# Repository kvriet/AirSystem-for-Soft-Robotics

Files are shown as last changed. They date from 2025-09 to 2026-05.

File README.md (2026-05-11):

# AirSystem for Soft Robotics
Modular Air System for Soft Robotics\
Designed and created by [C.M. van Riet](https://research.tue.nl/en/persons/cm-katrien-van-riet) - Summer 2025\
With thanks to d.search at Eindhoven University of Technology for their guidance.\
Special thanks to Geert van den Boomen for checking the schematics and debugging the circuits.

## The system
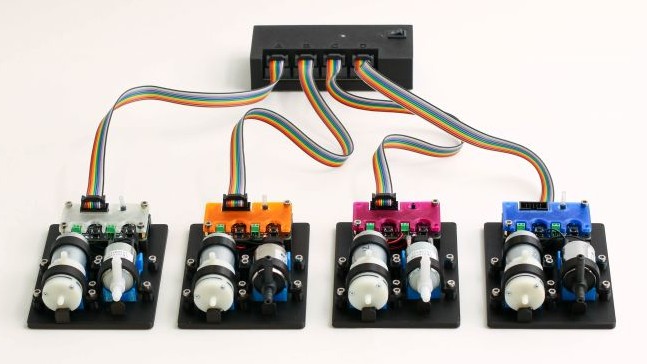
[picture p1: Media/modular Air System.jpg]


**AirSystem** was designed as a low-cost way to rapidly prototype with air, costing roughly €125 for the entire system. AirSystem consists of 1 controller and 4 pneumatic units. Each pneumatic unit contains one pump, one solenoid valve, and one pressure sensor. The board provides 12V power and as such, any pump or solenoid that requires 12V power can be attached to the unit board. 

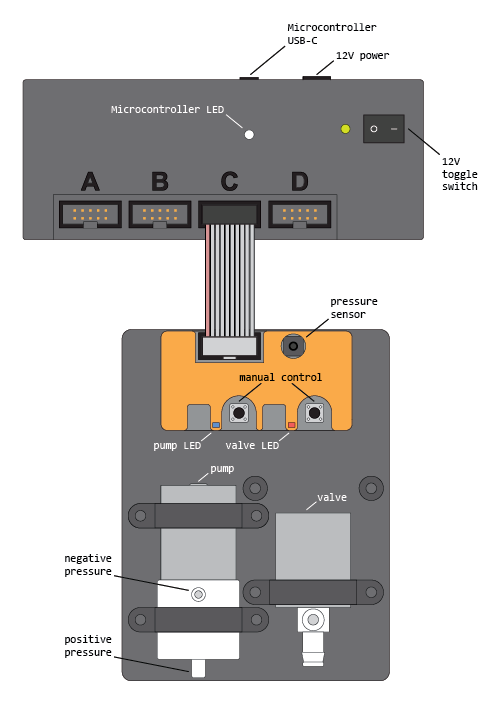
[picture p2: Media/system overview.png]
System overview


### Pneumatic Components
For the pneumatic board, easy-to-find components are used:
1. Pump 370A, 12V, 3.2LPM
2. Solenoid valve Skoocom SC0829GW, 12V
3. MCP-H10 pressure sensor, 0-200kPa, 3.3V

### Manual
A manual for AirSystem describes in detail how the system works and how the Arduino library can be installed: [AirSystem Manual](https://github.com/kvriet/AirSystem-for-Soft-Robotics/blob/main/Air%20System%20manual%20v1.4.pdf)
Users are free to connect the sensor, pump, and valve to their inflatables as desired. However, a sample pneumatic circuit is outlined in the manual, along with example Arduino sketches that work well with such a circuit.

## Arduino Library
The system is controlled by a Waveshare RP2040 Zero and can be programmed through the Arduino IDE with a custom library: [AirSystem](https://github.com/kvriet/AirSystem-for-Soft-Robotics/tree/main/Arduino%20library/AirSystem) This folder should be placed in the libraries folder of the Arduino folder. 

The library comes with 7 examples that showcase the abilities of **AirSystem**:
  1. Manual control
  2. Pressure reading
  3. Pump control
  4. Valve control
  5. Pump control without delay
  6. Haptic effects
  7. Object arrays

The video below shows such a haptic effect:

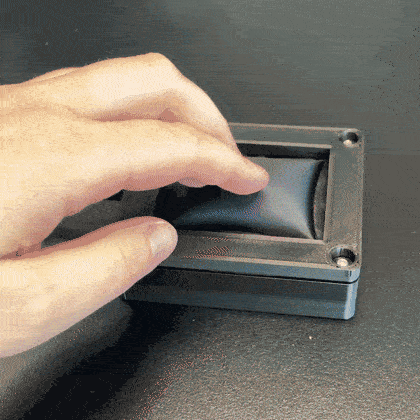
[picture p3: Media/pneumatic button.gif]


## Schematics and KiCAD Files
The schematics for this project and the KiCAD files can be found here: [KiCAD folder](https://github.com/kvriet/AirSystem-for-Soft-Robotics/tree/main/KiCAD).

## 3D Printing Files
The STLs for this project can be found here: [Design Files](https://github.com/kvriet/AirSystem-for-Soft-Robotics/tree/main/Design%20Files).
- The prints will fit most regular printers and can be printed out of PLA, 0.3 layer height, 4 perimeters (walls), 20% infill. The cushions for the pumps and solenoids are printed in TPU. These cushions can be replaced with some sponge (simple kitchen sponges work well) if TPU printing is not an option.
- To minimise vibrations and prevent the cases from sliding around on a hard surface, 6mm silicone feet are added to the bottom of control and follower cases.
- Any 4mm holes in the prints will require M3x4mm heated inserts to create screw holes. These can be inserted with a soldering iron at roughly 300 degrees Celsius. The other 3mm holes are self-tapping.

The screws needed for these cases are:

**Controller**
- 4x M3x10 or M3x20 (any length in between), flathead

**Follower**
- 4x M3x6 for the coloured cover
- 4x M3 spacer: 6mm height, 6mm thread
- 8x M3x10 for the clamps

## Limitations
- Although protection is implemented on the signal lines, the Waveshare RP2040 Zero sometimes dies when the IDC connector cable is plugged into the controller or follower when the RP2040 is still connected by USB C. For this reason, it is important to unplug the RP2040 before plugging in/out ribbon cables.
- Due to the above issue, I am looking into switching to the ESP32 C3 Zero (Pro). This board is equally cheap, but seems to be more robust. This board is currently not yet a drop-in replacement for the RP2040, although it can already be made to work if some soldering on the controller is reworked and the pin numbers in the library are updated. I will probably release KiCAD files for an ESP32 controller in the future. The follower boards will not be affected, although the resistor value in series with the mosfet might be updated (from 1k to 500R).
- The Skoocom solenoid valve is able to remain closed up to pressures of 100kPa, whereas the pump is able to deliver 150kPa. This means the valve will start leaking at pressures over 100kPa. In practice, this is not a major issue, as our projects rarely need pressures of over 100kPa (usually maxing out at 50kPa for haptic purposes). However, this overpressure might reduce valve longevity in the long run. In the future, a higher-pressure solenoid valve could be found, or a pump could be found that delivers max 100kPa. This would also allow for a lower-range pressure sensor to be used, the MCP-H10 0-100kPa, 3.3V. Switching to the 0-100kPa sensor would also double pressure measuring resolution.
- Currently no PID has been implemented in the library. As many inflatables or the tubing used are somewhat elastic, I have found that setting a target pressure (feedback loop sensor reading to pump power) is enough to achieve that pressure with a minimal offset. However, for more high-end applications, PID should be implemented.
- The Skoocom solenoid valve is not proportional. It is just open/closed. This means that controller deflation is a challenge. This can be worked around by turning on the pump simultaneously to opening the valve to reduce the air flowing out. Additionally, a resistor (very thin tube) could be connected to the valve outlet to reduce airflow out of the system. However, such a resistor also slows down response times when air does need to evacuate the system quickly. This is a trade-off for how cheap this entire system is.

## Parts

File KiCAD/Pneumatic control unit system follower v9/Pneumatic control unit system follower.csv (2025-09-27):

Reference | Value | Datasheet | Footprint | Qty | DNP
C1,C2,C3,C4,C7,C8,C11 | 100nF | ~ | Capacitor_SMD:C_0603_1608Metric_Pad1.08x0.95mm_HandSolder | 7
C5,C6,C9,C10 | 100uF | ~ | Capacitor_THT:CP_Radial_D6.3mm_P2.50mm | 4
D1,D3 | LED_Small | ~ | Diode_SMD:D_0805_2012Metric_Pad1.15x1.40mm_HandSolder | 2
D2,D4 | 1N4007 | http://www.vishay.com/docs/88503/1n4001.pdf | Diode_SMD:D_SMA_Handsoldering | 2
D5,D6 | 1N4148 | https://assets.nexperia.com/documents/data-sheet/1N4148_1N4448.pdf | Diode_SMD:D_MiniMELF_Handsoldering | 2
J1 | unit_1 | https://www.tinytronics.nl/en/cables-and-connectors/connectors/jst-compatible/jst-xh-6p-compatible-pcb-connector-male-90 | Library:JST_XH_S6B-XH-A-1_1x06_P2.50mm_Horizontal_5mm | 1
M1,M2 | Pump | ~ | TerminalBlock_Phoenix:TerminalBlock_Phoenix_MPT-0,5-2-2.54_1x02_P2.54mm_Horizontal | 2
Q1,Q2 | AO3400A | http://www.aosmd.com/pdfs/datasheet/AO3400A.pdf | Package_TO_SOT_SMD:SOT-23 | 2
R1,R4 | 680R | ~ | Resistor_SMD:R_0603_1608Metric_Pad0.98x0.95mm_HandSolder | 2
R2,R5 | 330R | ~ | Resistor_SMD:R_0603_1608Metric_Pad0.98x0.95mm_HandSolder | 2
R3,R6 | 100k | ~ | Resistor_SMD:R_0603_1608Metric_Pad0.98x0.95mm_HandSolder | 2
SW1,SW2 | SW_Push | ~ | Button_Switch_THT:SW_PUSH_6mm | 2
U1 | ~ |  | Library:MCP-H10 | 1

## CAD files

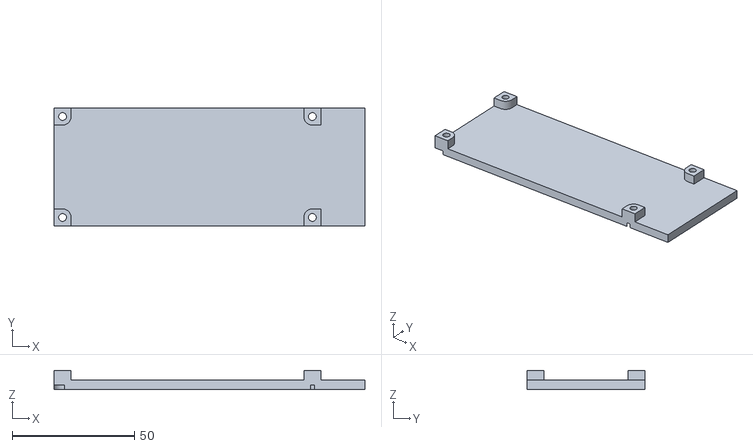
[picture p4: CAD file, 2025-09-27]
Design Files/bottom lid v2.2.stl
127.1 x 48.3 x 7.80

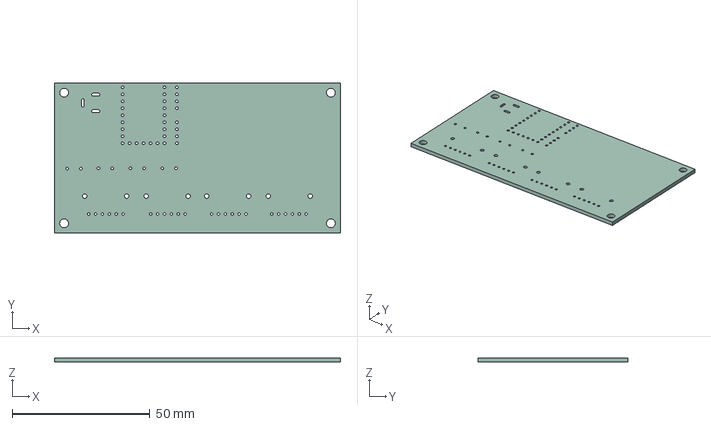
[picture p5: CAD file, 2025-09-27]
KiCAD/Pneumatic control unit system leader v9/Pneumatic control unit system.step
104.0 x 54.5 x 1.60 mm

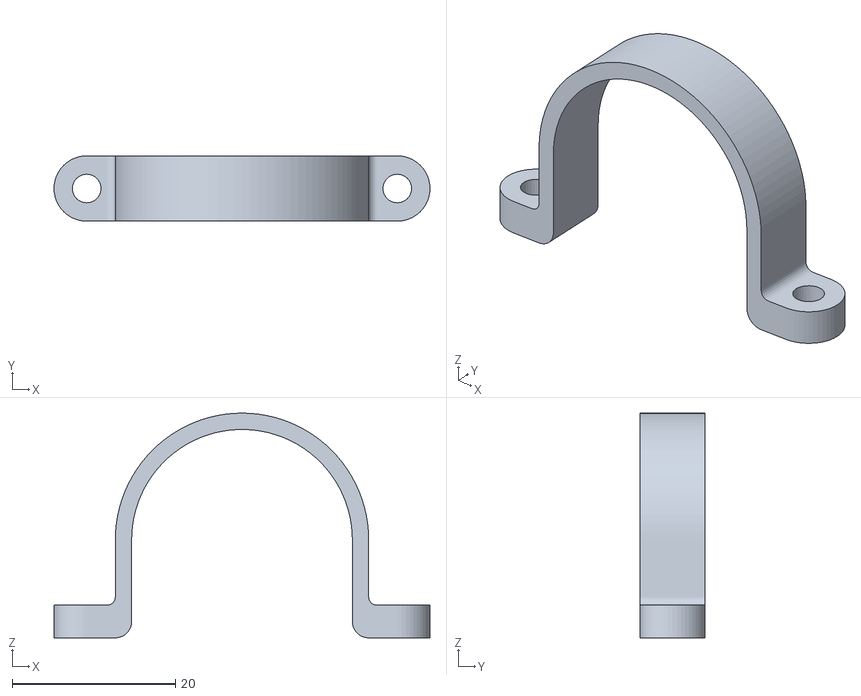
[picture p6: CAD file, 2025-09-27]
Design Files/clamp big v5.stl
46.0 x 8.00 x 27.5

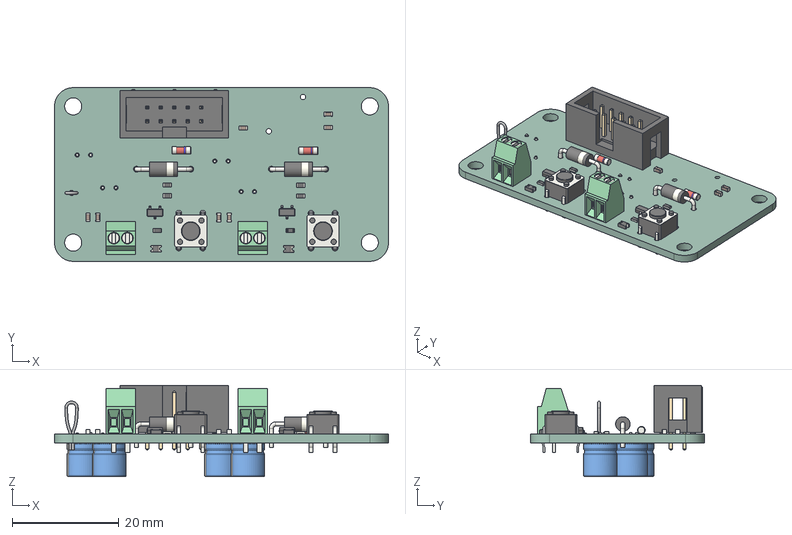
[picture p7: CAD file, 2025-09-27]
KiCAD/Pneumatic control unit system follower v9/follower v8.2.step
62.5 x 32.5 x 17.1 mm
R_0603_1608Metric x 6
D_MiniMELF_Standard x 2
D_DO-41_SOD81_P10.16mm_Horizontal x 2
SW_PUSH_6mm x 2
TestPoint_Loop_D2.50mm_Drill1.0mm
C_0603_1608Metric x 7
IDC_Header_2x05_P254mm_Vertical
TerminalBlock_Phoenix_MPT_05_2_254_1x02_P254mm_Horizontal x 2
SOT_23 x 2
D_0805 x 2
CP_Radial_D63mm_P250mm x 4
Pneumatic control unit system_PCB

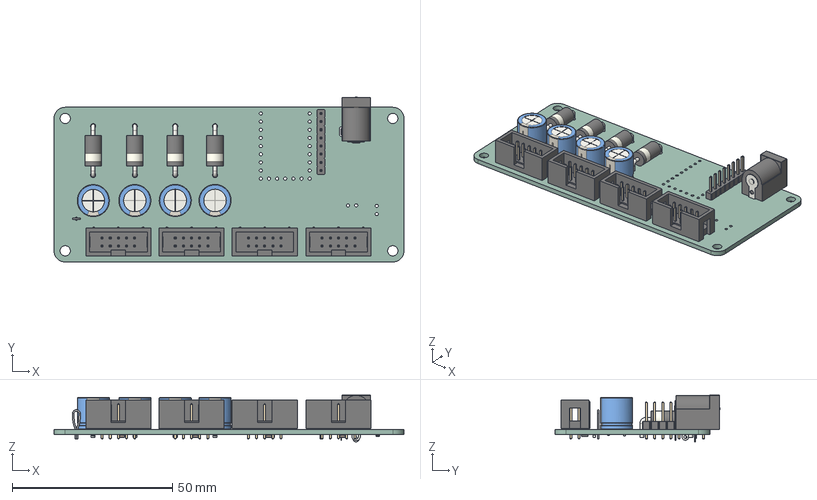
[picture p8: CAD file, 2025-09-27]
KiCAD/Pneumatic control unit system leader v9/Leader v9.step
109.1 x 51.5 x 14.6 mm
IDC_Header_2x05_P254mm_Vertical x 4
TestPoint_Loop_D2.50mm_Drill1.0mm
CP_Radial_D100mm_P500mm x 4
D_DO-201AD_P15.24mm_Horizontal x 4
PinHeader_1x08_P254mm_Vertical
BarrelJack_Horizontal
R_0805_2012Metric
C_0603_1608Metric x 5
Pneumatic control unit system_PCB

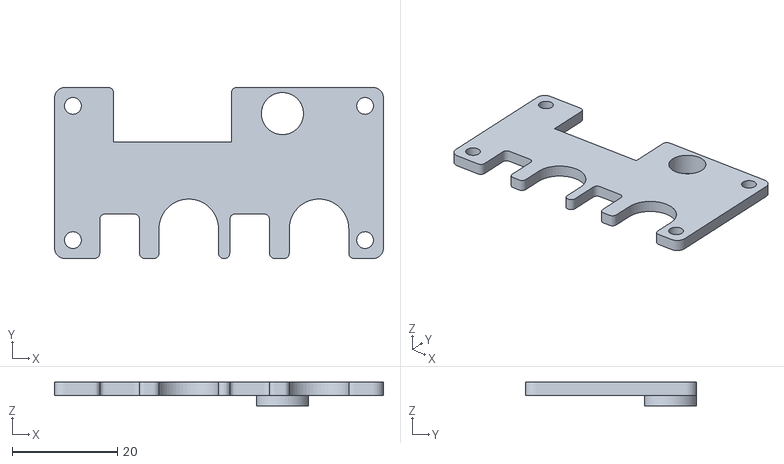
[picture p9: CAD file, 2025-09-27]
Design Files/top lid PLA v2.2.stl
62.5 x 32.5 x 4.50

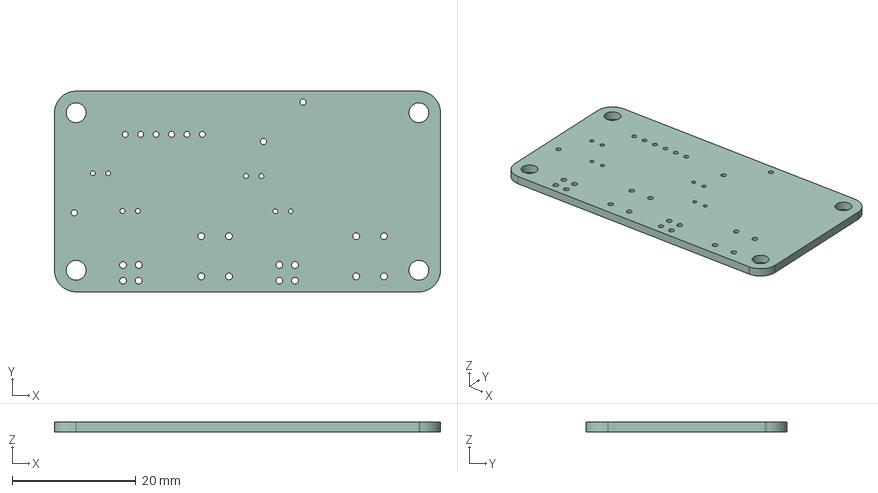
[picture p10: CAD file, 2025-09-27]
KiCAD/Pneumatic control unit system follower v9/Pneumatic control unit system broad.step
62.5 x 32.5 x 1.60 mm

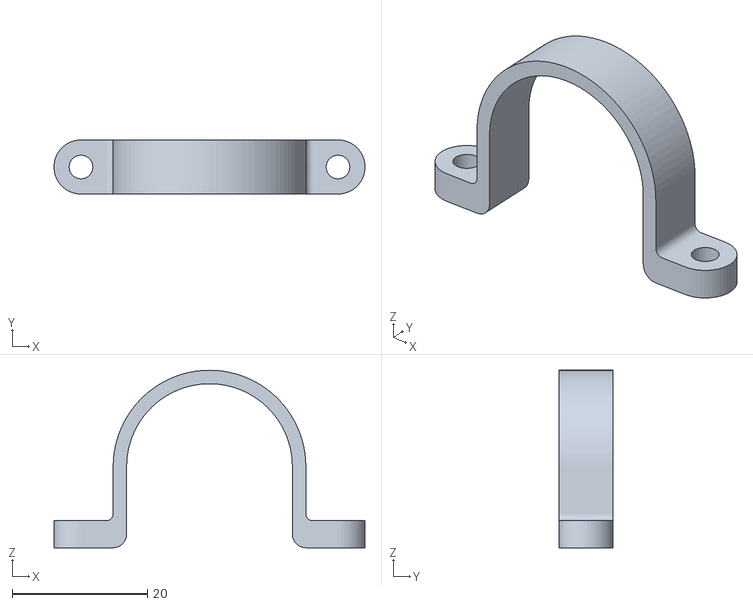
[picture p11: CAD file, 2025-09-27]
Design Files/clamp small v5.stl
46.0 x 8.00 x 26.2

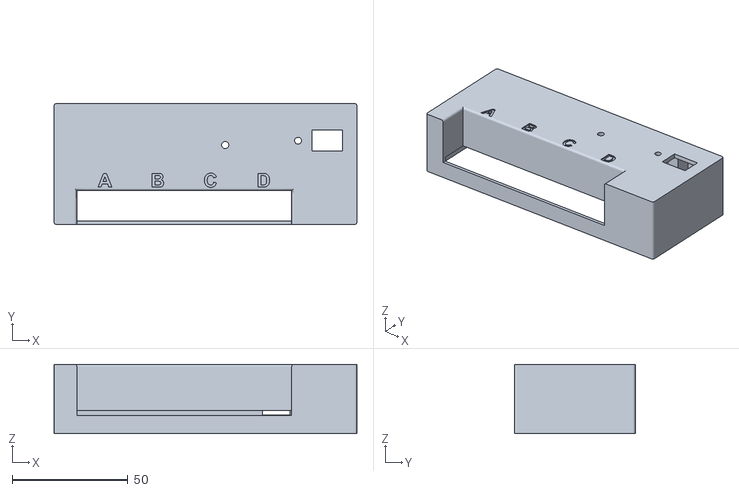
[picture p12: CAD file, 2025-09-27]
Design Files/top lid v2.3.stl
131.1 x 52.2 x 30.0

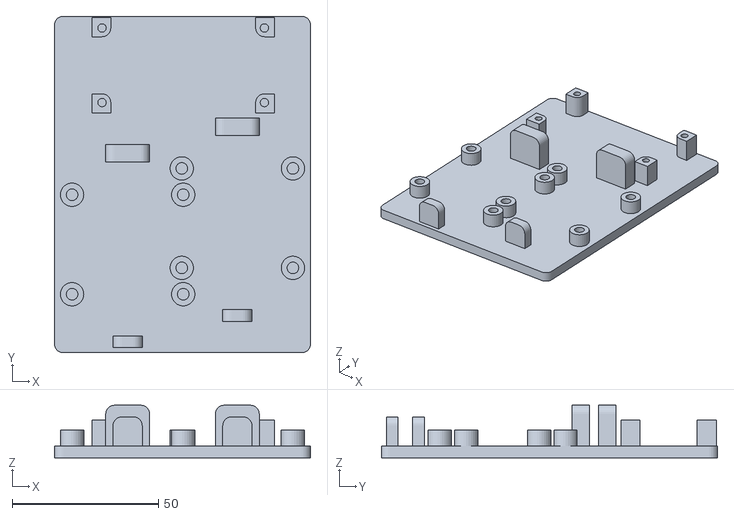
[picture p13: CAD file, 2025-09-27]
Design Files/case base v2.1.stl
87.5 x 115.0 x 18.0

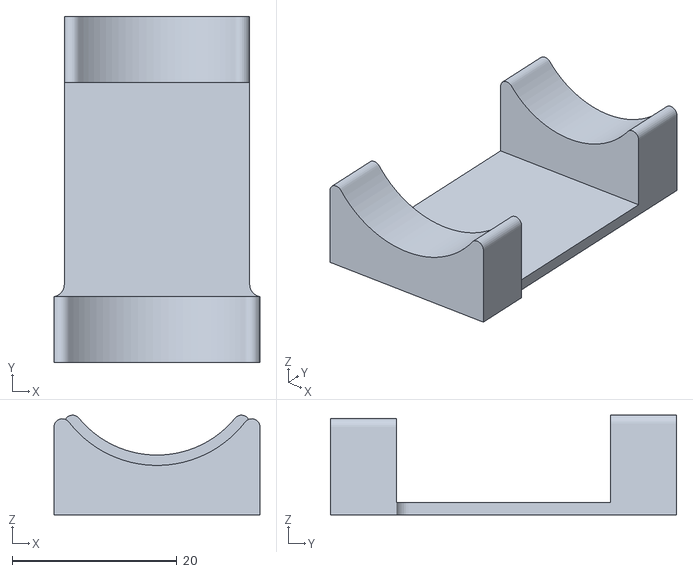
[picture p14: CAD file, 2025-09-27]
Design Files/cushion connected v2.stl
25.0 x 42.0 x 12.1

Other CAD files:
KiCAD/Pneumatic control unit system follower v9/follower v8.step

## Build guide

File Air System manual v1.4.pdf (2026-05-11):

# AIR CONTROL SYSTEM

# MANUAL

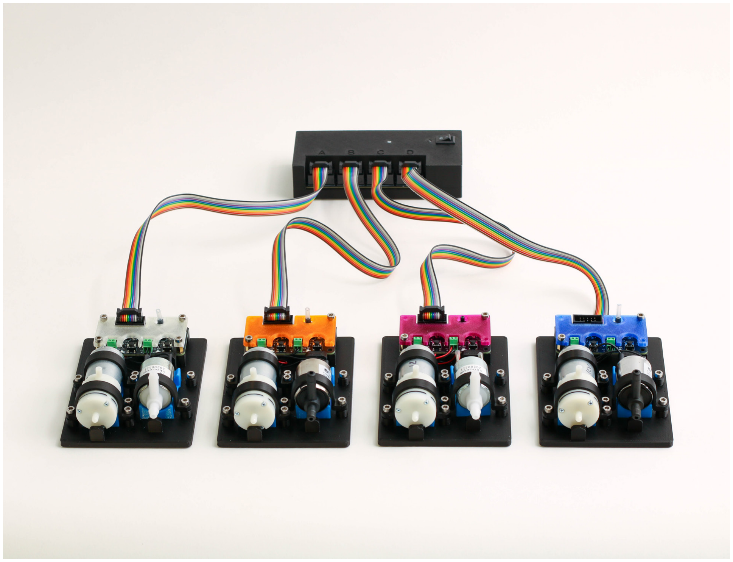
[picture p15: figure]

C.M. van Riet - May '26 - v1.4

# OVERVIEW

Controller
The controller can control up to 4 pneumatic units. It is powered by a 12V power supply and a Waveshare RP2040 PiZero, which can be

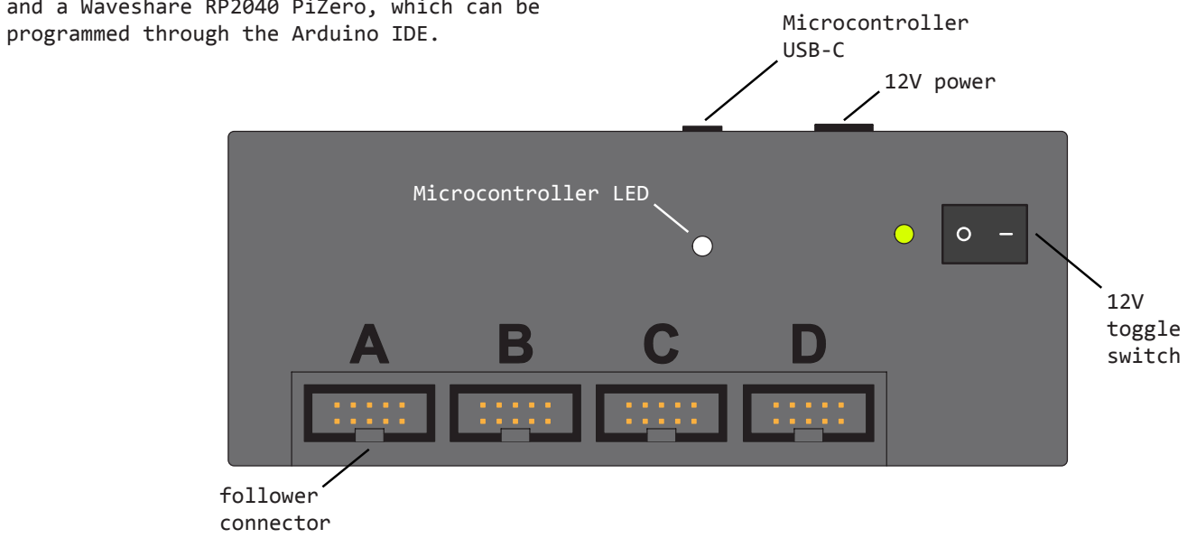
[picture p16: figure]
programmed through the Arduino IDE.; 12V power; Microcontroller USB-C; follower connector; 12V toggle switch; Microcontroller LED

Pneumatic unit

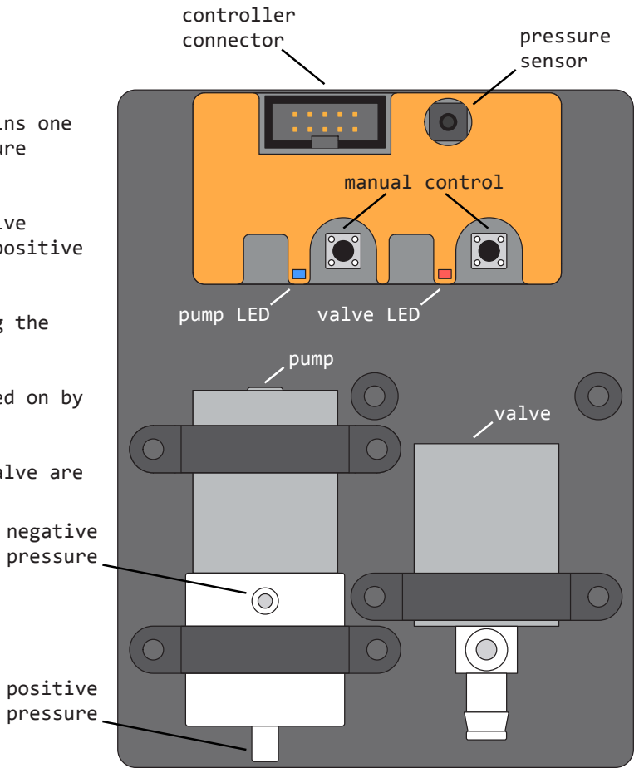
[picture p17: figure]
controller; connector; pressure; sensor; pump LED; pump; valve; valve LED; manual control; positive pressure; negative pressure

Each pneumatic unit (or follower) contains one pump, one solenoid valve, and one pressure sensor.

The pump can provide positive and negative pressure (vacuum). You will mainly use positive pressure for the pneumatic buttons.

The valve is normally closed. Activating the valve opens it.

The pump and valve can be manually turned on by pressing the buttons.

The LEDs indicate whether the pump or valve are turned on.

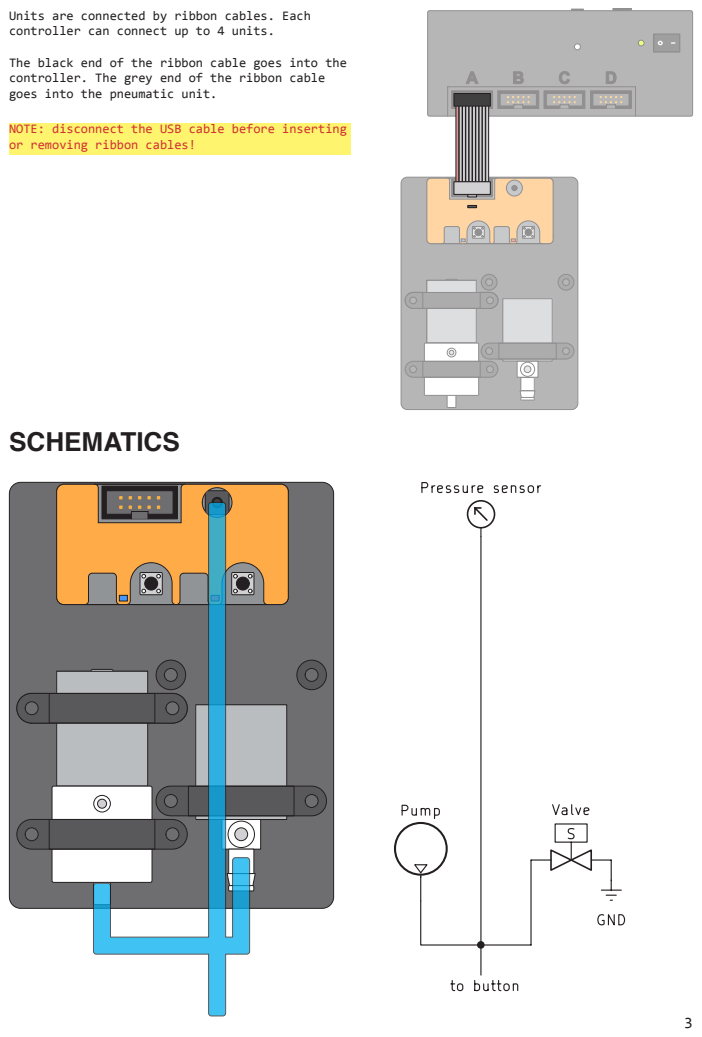
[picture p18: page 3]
SCHEMATICS

Units are connected by ribbon cables. Each
controller can connect up to 4 units.
The black end of the ribbon cable goes into the
controller. The grey end of the ribbon cable
goes into the pneumatic unit.

NOTE: disconnect the USB cable before inserting
or removing ribbon cables!

# INSTALLING THE BOARD

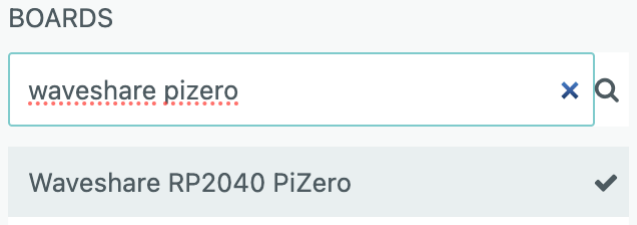
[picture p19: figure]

# INSTALLING THE ARDUINO LIBRARY

Before you can upload sketches to the AirSystem, you need to install the correct microcontroller board. The system uses the Waveshare RP2040 PiZero board.

Open Arduino IDE. Go to Settings (ctrl + , or command + ,).
In the Additional boards manager URLS, add this link:
https://github.com/earlephilhower/arduino-pico/releases/download/4.5.2/package_rp2040_index.json
Now go to Boards Manager:

Search for and install "Raspberry Pi Pico/RP2040/RP2035" by Earle F. boards.

To connect to the board, click the board connector:

Search for "waveshare pizero" and select the "Waveshare RP2040 PiZero":

Before you can make Arduino sketches using the AirSystem library, you need to install the library.

To do this, put the AirSystem folder (unzipped) into your Arduino libraries folder:

Arduino/
└── libraries/
└── AirSystem/
├── AirSystem.h
├── AirSystem.cpp
└── examples/

Whenever you want to use the library, don't forget to call it at the top of your sketch: #include <AirSystem.h>

Also don't forget to initialise the pins in the setup loop:
AirSystem_begin(); // Initialise the pins

# PROGRAMMING

The AirSystem library is an object-oriented library that provides three types of objects:
- Pump → controls an air pump using PWM (0–100% power).
- Valve → controls a solenoid valve (open/close).
- Sensor → reads air pressure from a pressure sensor.
Accessing Objects
You can access objects in two ways:
By name (if you created them individually):
- PumpA.set(50); | // Set PumpA to 50% power
- ValveB.open(); | // Open ValveB
- float p = SensorC.read(); // Read SensorC pressure

By array index:
- pumps[0].set(50); | // PumpA
- valves[1].close(); | // ValveB
- float p = sensors[2].read(); // SensorC Functions
Pump
- set(percentage) → Set pump power (0–100%).
- off() | → Turn pump off (same as set(0)).
- on() | → Turn pump fully on (100%).

Valve
- open() | → Open the valve.
- close() | → Close the valve.

Sensor
- read() | → Returns the current pressure in kPa (kiloPascal).

# STEP 1: MANUAL CONTROL

The pump and valves can be operated through the push buttons on the follower unit.

Upload the following code. It will not activate the pumps or valves. Instead you can press the pump and valve buttons to inflate and deflate your pneumatic button.

/*
AirSystem Demo Sketch

Author: C.M. van Riet
Library: AirSystem
Date: September 2025

Objects can be called in 2 ways:
- pumpA, valveB, sensorC (named)
- pumps[0], valves[1], sensors[2] (array-based)

Functions available in this library:
- Initialize the system with AirSystem_begin()
- Control pumps with .set(percentage), on(), and .off()
- Control valves with .open() and .close()
- Read pressure from sensors with .read()

Hardware:
- Designed for a maximum of 4 pumps, 4 valves, and 4 sensors
- Pin mappings are fixed in the library (see AirSystem.h)

Notes:
- Make sure to include the AirSystem.h library at the top of your sketch (#include <AirSystem.h>)
- This example can be found under File > Examples > AirSystem > 1_First_demo.

Board:
- Add this link to preferences, Additional boards manager URLs: https://github.com/earlephilhower/arduino-pico/releases/download/4.5.2/package_rp2040_index.json
- Install "Raspberry Pi Pico/RP2040/RP2035" by Earle F. boards
- Connect to Waveshare RP2040 PiZero
*/

#include <AirSystem.h>

void setup() {
Serial.begin(9600);
AirSystem_begin(); // Initialise the pins
pumpA.off(); | // Pump off
valveA.close(); | // Close valve
}

void loop() {
// This loop is empty
// You can turn on the pump and valve by pressing // the buttons on the board of the unit
}

#include <AirSystem.h>

void setup() {
Serial.begin(9600);
AirSystem_begin(); // Initialise the pins
pumpA.off(); | // Pump off
valveA.close(); | // Close valve
}

void loop() {
float pressure = sensorA.read();
Serial.print(0); // Lower limit in Serial Plotter Serial.print("\t"); // Print a tab Serial.print(200); // Upper limit in Serial Plotter Serial.print("\t"); // Print a tab Serial.println(pressure);

delay(10);
}

# STEP 2: PRESSURE READINGS

To get the pressure sensor value, use the read() function.

Upload the following code. Use the push buttons to inflate and deflate your pneumatic button and use the Serial Monitor (Ctrl+Shift+M) and Serial Plotter to watch the pressure value fluctuate.

# STEP 3: PUMP CONTROL

The code below turns the pump on and off. Don't connect the pump to your pneumatic button yet!

- Try to change the delay values. How does the pump turning on and off change?
- Try to change the value in the set() function. How does it change the pump behaviour?
- If you connect the pump to your pneumatic button, will it only inflate? Or also deflate?

#include <AirSystem.h>

void setup() {
Serial.begin(9600);
AirSystem_begin(); // Initialise the pins
pumpA.off(); | // Pump off
valveA.close(); | // Close valve
}

void loop() {
pumpA.set(50);
Serial.println("Pump set to 50% intensity");

delay(2000);

pumpA.off();
Serial.println("Pump turned off");

delay(2000);
}

#include <AirSystem.h>

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

void loop() {
valveA.close();
pumpA.set(25);
Serial.println("Valve closed and pump set to 25%");

delay(1000);

valveA.open();
pumpA.off();
Serial.println("Valve opened and pump turned off");

delay(2000);
}

# STEP 4: VALVE CONTROL

The code below is similar to the code in step 3, but it adds valve control. Now your pneumatic button will inflate and deflate.

- Play with the pump power percentage and the timing (delay) to get an aesthetically pleasing inflation and deflation of your pneumatic button.

# STEP 5: PUMP WITHOUT DELAY

In step 4 we turned the pump on and off. We used the delay() function for this, but this freezes up the entire program; you can't do anything else during the delay. To fix this, the code below gives you pump control without delay. This is similar to the 'Blink without delay' example in the Arduino library.

For this to work, we use a general timer (currentMillis) to keep track of time.

// Pump without delay based on the code by David A. Mellis

#include <AirSystem.h>

// Variables will change:
int pumpState = LOW; // pumpState used to set the pump on/off

// Generally, you should use "unsigned long" for variables that hold time // The value will quickly become too large for an int to store
unsigned long previousMillis = 0; // will store last time LED was updated

// Constants won't change:
const long interval = 1000; // interval at which to blink (milliseconds) // Blink here means turn the pump on and off

#include <AirSystem.h>

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

void loop() {
// Here is where you'd put code that needs to be running all the time.

// Get the current elapsed milliseconds from the start of the sketch
unsigned long currentMillis = millis();

if (currentMillis - previousMillis >= interval) {
// This if-statement checks if the current time is bigger than the previous time - interval // So check if the interval time (1 second) has elapsed

previousMillis = currentMillis;

// If the pump is off, turn it on and vice-versa:
if (pumpState == LOW) {
pumpState = HIGH;
pumpA.set(50); // Set pump to 50% valveA.close(); // Close valve
} else {
pumpState = LOW;
pumpA.off(); // Turn pump off valveA.open(); // Open valve
}
}
Serial.print(currentMillis); Serial.print("\t");
Serial.print(previousMillis); Serial.print("\t");
Serial.printn(interval);
}

#include <AirSystem.h>

int setpoint = 30; | // The target pressure (kPa) for the button
int offset = 2; | // Optional: how much higher the target pressure can be before
// pump turns off (to prevent pump jitter)
int threshold = 45; | // The pressure at which the buttons 'snaps' down
int counter_number = 3; | // For how many loops the button empties
int counter = 0; | // We start our haptic effect counter at 0
bool doHapticEffect = false; | // Currently don't do the haptic effect yet

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

void loop() {
float pressure = sensorA.read();

// Pump control
if (doHapticEffect == false) {
// If we're not doing the haptic effect:
if (pressure < setpoint) {
// If the pressure is not at the target level, keep pumping pumpA.set(100); // Set pump to 100%
valveA.close(); // Keep valve closed
} else if (pressure >= setpoint + offset) {
// If target pressure has been reached (+ offset value), turn pump off pumpA.off();
}
}

if (pressure > threshold) {
// If the pressure meets haptic effect threshold, set doHapticEffect to true doHapticEffect = true;
}

if (doHapticEffect == true) {
// If we have to do the haptic effect, turn off pump and open valve pumpA.off();
valveA.open();
counter++; // Increment counter
if (counter > counter_number) {
// After 3 cycles, the haptic effect resets and pressure will need to meet threshold again doHapticEffect = false;
counter = 0;
}
}
delay(10);
}

# STEP 6: HAPTIC EFFECT

Now that we are familiar with the basics of the Air System, we can start playing with haptic effects. In the code below, the pump produces a certain target pressure (setpoint). When you press your pneumatic button, and you reach a certain threshold pressure, the valve suddenly opens, thereby producing a snapping effect in the button.

# STEP 7: OBJECT ARRAYS

In the previous examples we worked with named objects for the pump, valve, and sensor. However, you can also directly address these objects within they object array. This can be useful if you want to loop through the objects. The code below shows you how to access:
- Pumps: pumps[i]
- Valves: valves[i]
- Sensors: sensors[i]

#include <AirSystem.h>

void setup() {
Serial.begin(9600);
AirSystem_begin(); // Initialise the pins pumps[0].off(); // Pump A off valves[0].close(); // Close valve A
}

void loop() {
// Close valve A and set pump A to 25% valves[0].close();
pumps[0].set(25);
delay(1000);

// Get pressure sensor A value and print float pressure = sensors[0].read(); Serial.println(pressure);

// Open valve A and turn pump A off valves[0].open();
pumps[0].off();
delay(2000);
}

PumpA = 15
PumpB = 13
PumpC = 11
PumpD = 9

ValveA = 14
ValveB = 12
ValveC = 10
ValveD = 8

SensorA = 29
SensorB = 28
SensorC = 27
SensorD = 26

LED_BUILTIN = 16 (WS2812, RGB)

# PIN OVERVIEW

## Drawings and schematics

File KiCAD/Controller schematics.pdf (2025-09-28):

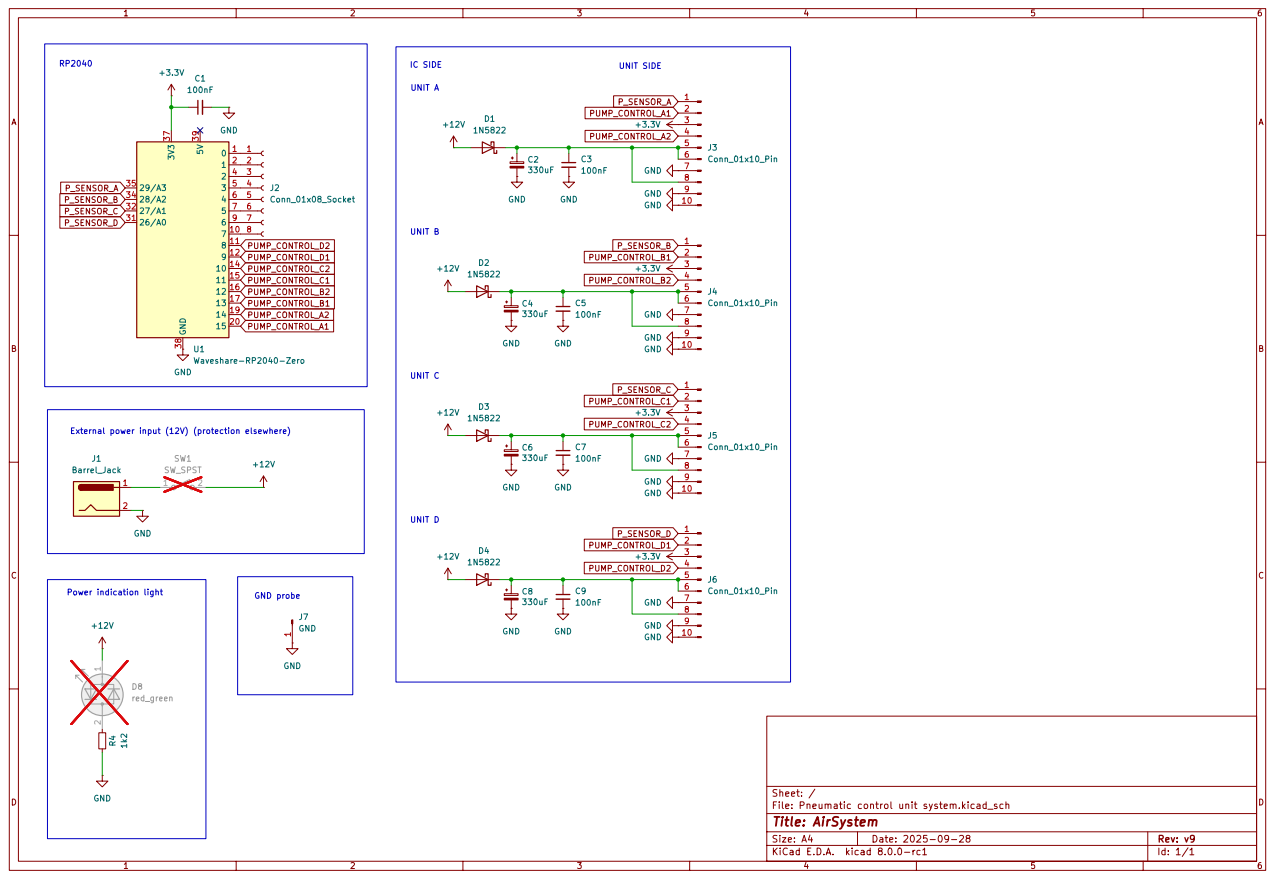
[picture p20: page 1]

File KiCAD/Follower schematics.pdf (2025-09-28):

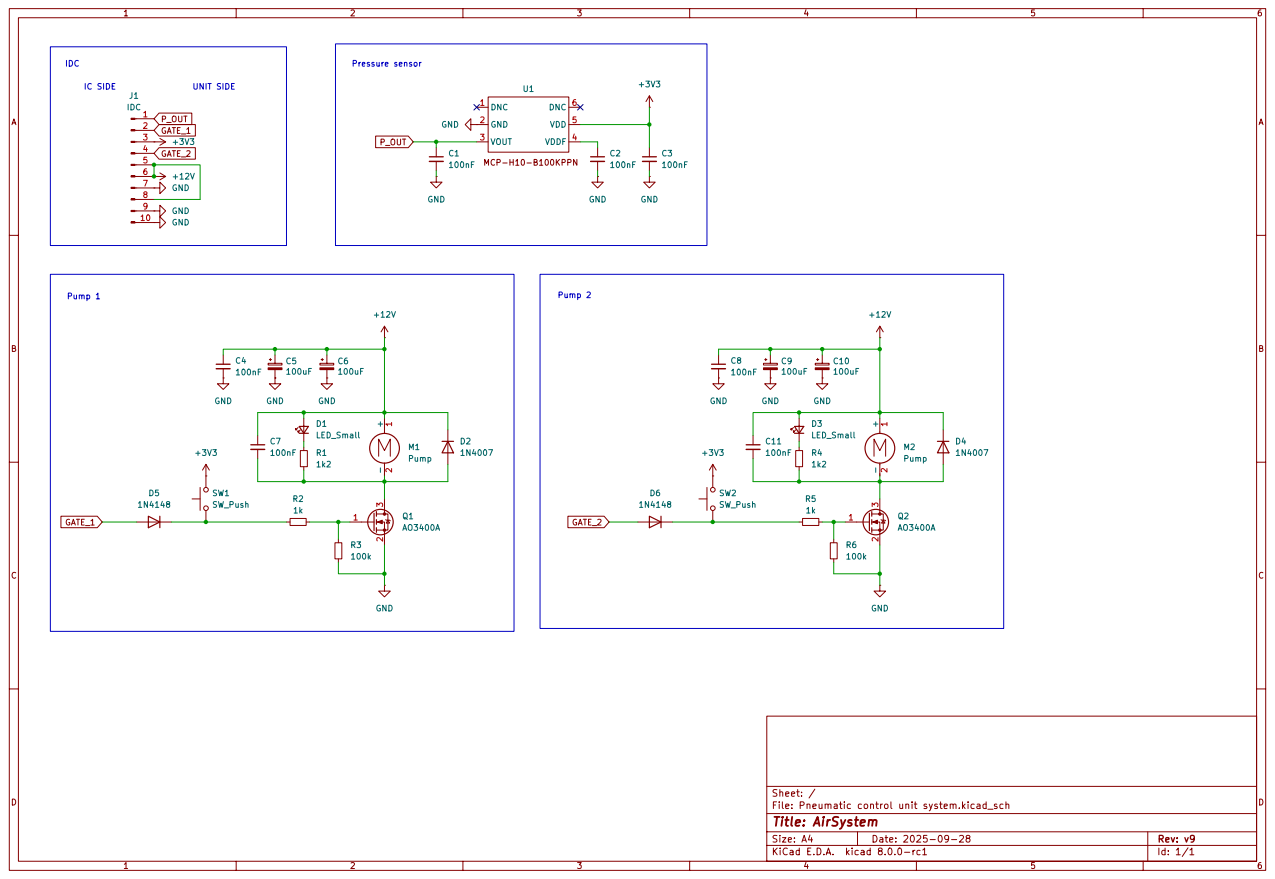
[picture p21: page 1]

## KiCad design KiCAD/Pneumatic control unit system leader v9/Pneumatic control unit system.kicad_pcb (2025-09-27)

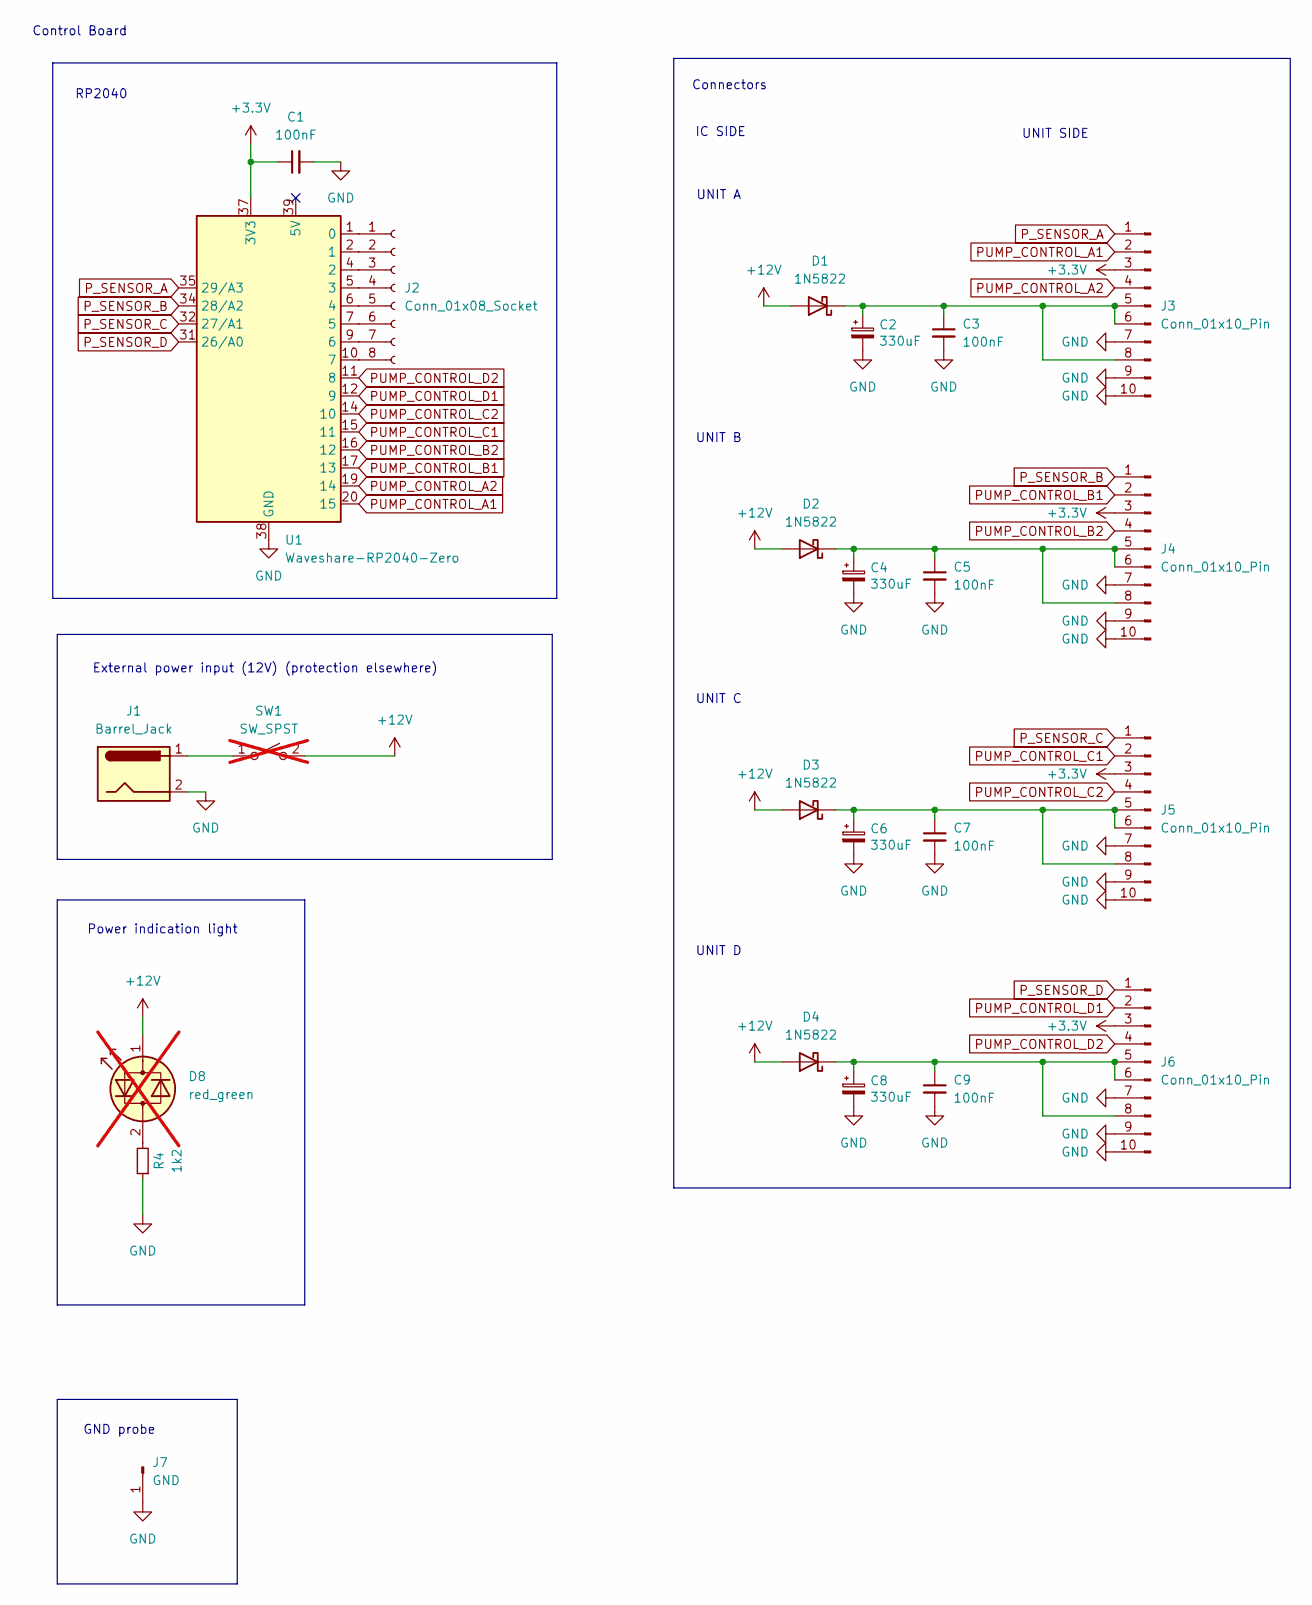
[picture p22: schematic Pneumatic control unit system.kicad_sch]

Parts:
C1, C3, C5, C7, C9: 100nF; C_0603_1608Metric_Pad1.08x0.95mm_HandSolder
C2, C4, C6, C8: 330uF; CP_Radial_D10.0mm_P5.00mm
D1, D2, D3, D4: 1N5822; D_DO-201AD_P15.24mm_Horizontal
D8: red_green; PinHeader_1x02_P2.54mm_Vertical; not fitted
J1: Barrel_Jack; BarrelJack_Horizontal
J2: Conn_01x08_Socket; PinHeader_1x08_P2.54mm_Vertical
J3, J4, J5, J6: Conn_01x10_Pin; IDC-Header_2x05_P2.54mm_Vertical
J7: GND; TestPoint_Loop_D2.50mm_Drill1.0mm
R4: 1k2; R_0805_2012Metric_Pad1.20x1.40mm_HandSolder
SW1: SW_SPST; PinHeader_1x02_P2.54mm_Vertical; not fitted
U1: Waveshare-RP2040-Zero; Waveshare_RP2040_Zero

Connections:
+3.3V: C1.1, J3.3, J4.3, J5.3, J6.3, U1.37 (3V3)
+12V: D1.2 (A), D2.2 (A), D3.2 (A), D4.2 (A), D8.1 (KA), SW1.2 (B)
GND: C1.2, C2.2, C3.2, C4.2, C5.2, C6.2, C7.2, C8.2, C9.2, J1.2, J3.7, J3.9, J3.10, J4.7, J4.9, J4.10, J5.7, J5.9, J5.10, J6.7, J6.9, J6.10, J7.1, R4.1, U1.38 (GND); also elsewhere on the board
unnamed: C2.1, C3.1, D1.1 (K), J3.5, J3.6, J3.8
unnamed: C4.1, C5.1, D2.1 (K), J4.5, J4.6, J4.8
unnamed: C6.1, C7.1, D3.1 (K), J5.5, J5.6, J5.8
unnamed: C8.1, C9.1, D4.1 (K), J6.5, J6.6, J6.8
unnamed: D8.2 (AK), R4.2
unnamed: J2.1, U1.1 (0)
unnamed: J2.2, U1.2 (1)
unnamed: J2.3, U1.4 (2)
unnamed: J2.4, U1.5 (3)
unnamed: J2.5, U1.6 (4)
unnamed: J2.6, U1.7 (5)
unnamed: J2.7, U1.9 (6)
unnamed: J2.8, U1.10 (7)
unnamed: J1.1, SW1.1 (A)
PUMP_CONTROL_A1: J3.2, U1.20 (15)
PUMP_CONTROL_A2: J3.4, U1.19 (14)
PUMP_CONTROL_B1: J4.2, U1.17 (13)
PUMP_CONTROL_B2: J4.4, U1.16 (12)
PUMP_CONTROL_C1: J5.2, U1.15 (11)
PUMP_CONTROL_C2: J5.4, U1.14 (10)
PUMP_CONTROL_D1: J6.2, U1.12 (9)
PUMP_CONTROL_D2: J6.4, U1.11 (8)
P_SENSOR_A: J3.1, U1.35 (29/A3)
P_SENSOR_B: J4.1, U1.34 (28/A2)
P_SENSOR_C: J5.1, U1.32 (27/A1)
P_SENSOR_D: J6.1, U1.31 (26/A0)

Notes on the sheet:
UNIT D
UNIT SIDE
Power indication light
UNIT C
External power input (12V) (protection elsewhere)
UNIT A
RP2040
Connectors
IC SIDE
Control Board
UNIT B
GND probe

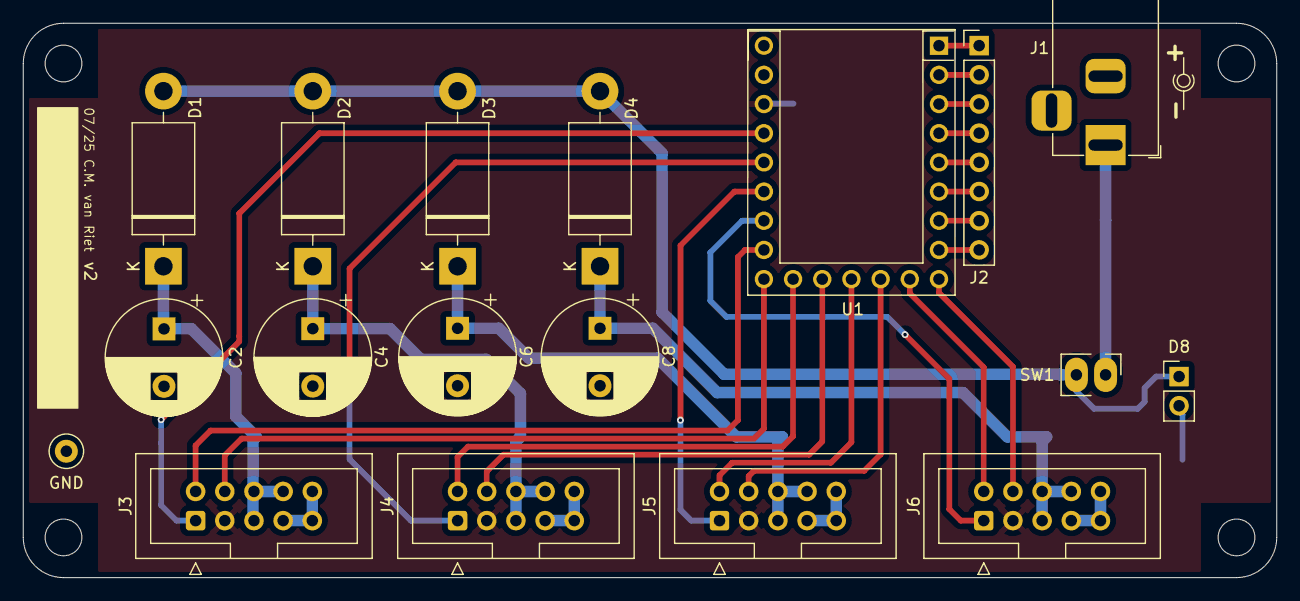
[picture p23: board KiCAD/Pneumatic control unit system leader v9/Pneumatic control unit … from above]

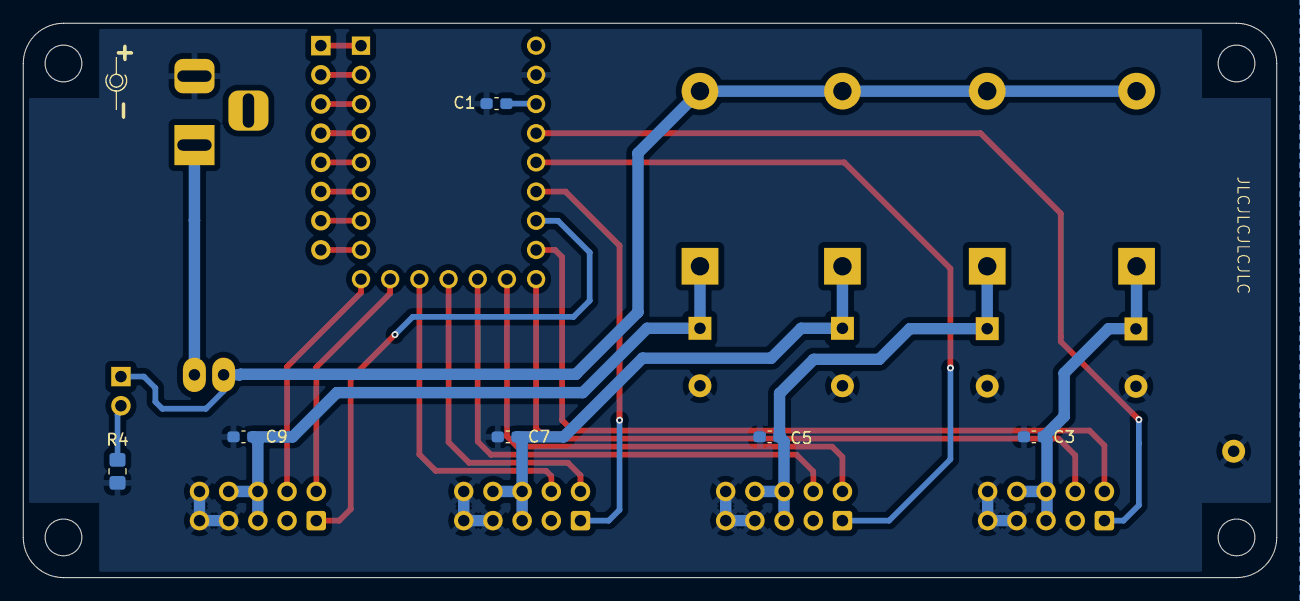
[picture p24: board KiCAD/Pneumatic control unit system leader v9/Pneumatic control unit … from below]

Board: 2 copper layers, 109.1 x 48.2 mm, 24 parts (6 on the bottom side), 29 nets.

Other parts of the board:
GND: GND; TestPoint_Loop_D2.50mm_Drill1.0mm

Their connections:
GND: GND.1; also elsewhere on the board

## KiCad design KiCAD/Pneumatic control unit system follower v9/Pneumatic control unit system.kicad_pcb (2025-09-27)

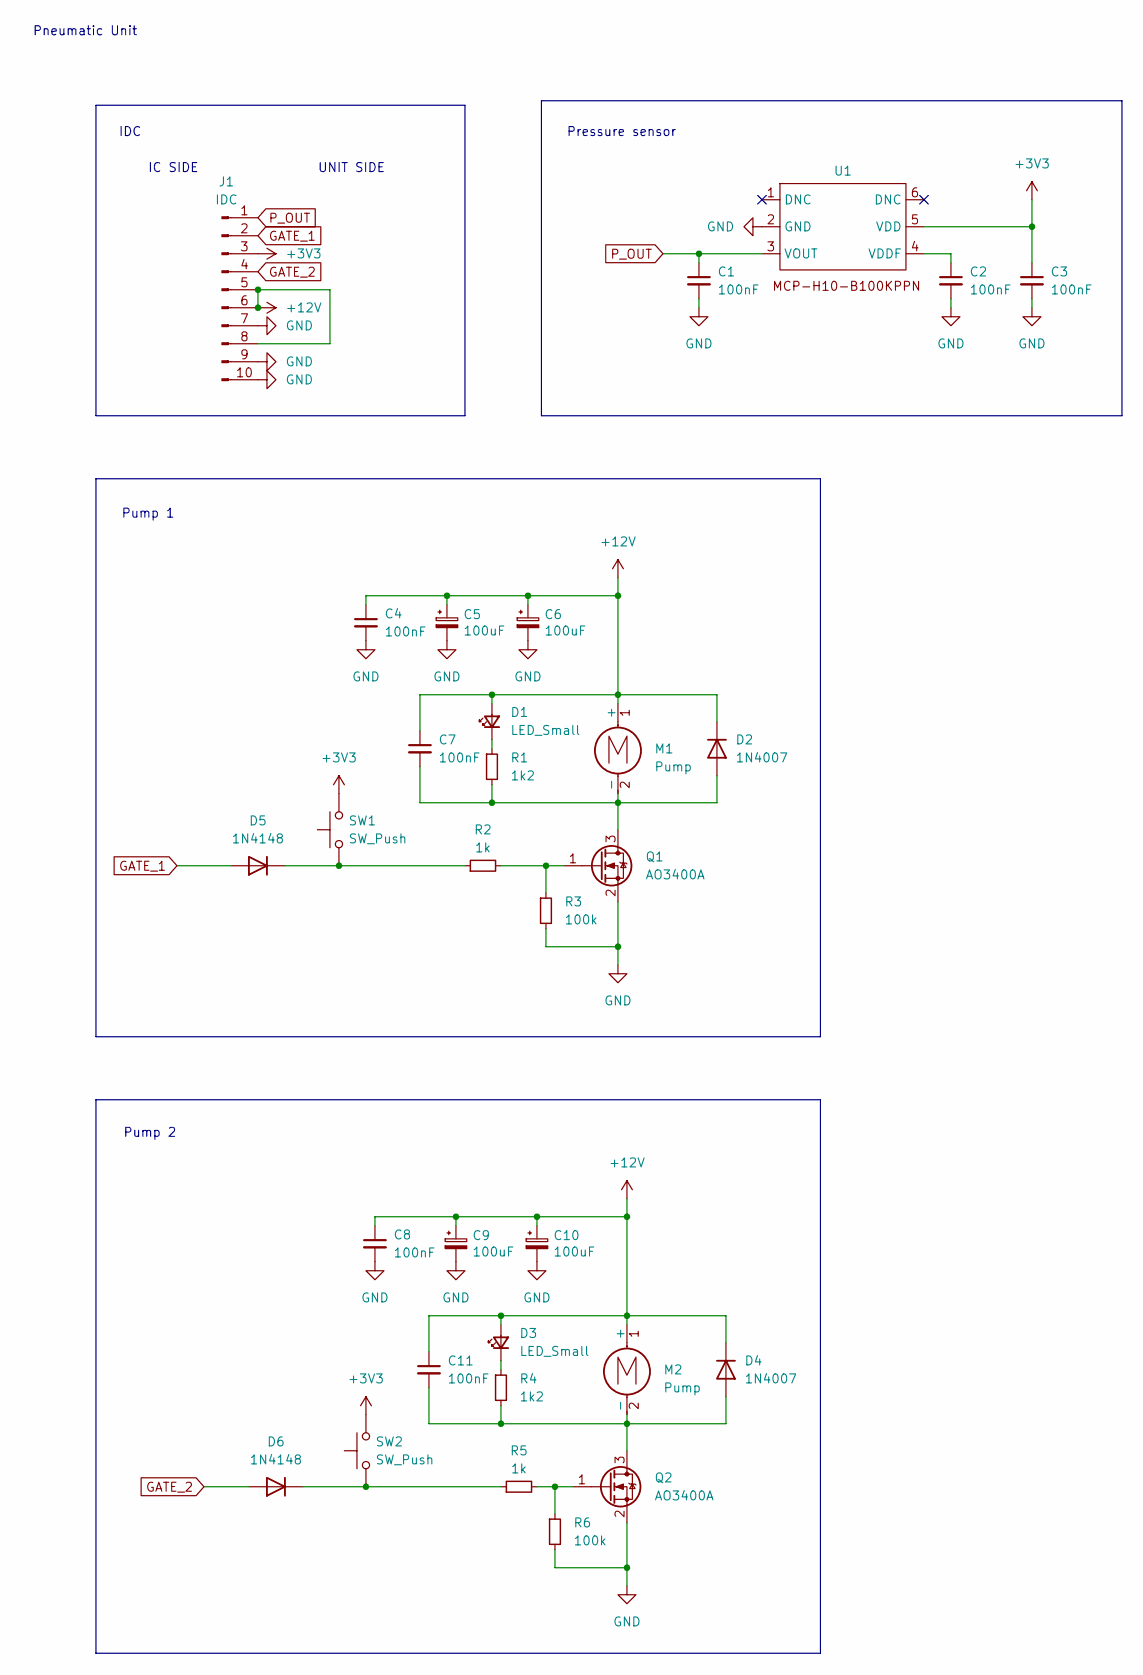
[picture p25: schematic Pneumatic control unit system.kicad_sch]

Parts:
C1, C2, C3, C4, C7, C8, C11: 100nF; C_0603_1608Metric_Pad1.08x0.95mm_HandSolder
C5, C6, C9, C10: 100uF; CP_Radial_D6.3mm_P2.50mm
D1, D3: LED_Small; D_0805_2012Metric_Pad1.15x1.40mm_HandSolder
D2, D4: 1N4007; D_DO-41_SOD81_P10.16mm_Horizontal
D5, D6: 1N4148; D_DO-35_SOD27_P7.62mm_Horizontal
J1: IDC; IDC-Header_2x05_P2.54mm_Vertical
M1, M2: Pump; TerminalBlock_Phoenix_MPT-0,5-2-2.54_1x02_P2.54mm_Horizontal
Q1, Q2: AO3400A; SOT-23
R1, R4: 1k2; R_0603_1608Metric_Pad0.98x0.95mm_HandSolder
R2, R5: 1k; R_0603_1608Metric_Pad0.98x0.95mm_HandSolder
R3, R6: 100k; R_0603_1608Metric_Pad0.98x0.95mm_HandSolder
SW1, SW2: SW_Push; SW_PUSH_6mm
U1: MCP-H10

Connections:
+3V3: C3.1, J1.3, SW1.2, SW2.2, U1.5 (VDD)
+12V: C4.1, C5.1, C6.1, C7.1, C8.1, C9.1, C10.1, C11.1, D1.2 (A), D2.1 (K), D3.2 (A), D4.1 (K), J1.5, J1.6, J1.8, M1.1 (+), M2.1 (+)
GATE_1: D5.2 (A), J1.2
GATE_2: D6.2 (A), J1.4
GND: C1.2, C2.2, C3.2, C4.2, C5.2, C6.2, C8.2, C9.2, C10.2, J1.7, J1.9, J1.10, Q1.2 (S), Q2.2 (S), R3.2, R6.2, U1.2 (GND); also elsewhere on the board
unnamed: D1.1 (K), R1.1
unnamed: C7.2, D2.2 (A), M1.2 (-), Q1.3 (D), R1.2
unnamed: D3.1 (K), R4.1
unnamed: C11.2, D4.2 (A), M2.2 (-), Q2.3 (D), R4.2
unnamed: D5.1 (K), R2.1, SW1.1
unnamed: D6.1 (K), R5.1, SW2.1
unnamed: Q1.1 (G), R2.2, R3.1
unnamed: Q2.1 (G), R5.2, R6.1
unnamed: C2.1, U1.4 (VDDF)
P_OUT: C1.1, J1.1, U1.3 (VOUT)

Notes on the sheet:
Pump 2
IC SIDE
Pneumatic Unit
Pump 1
IDC
UNIT SIDE
Pressure sensor

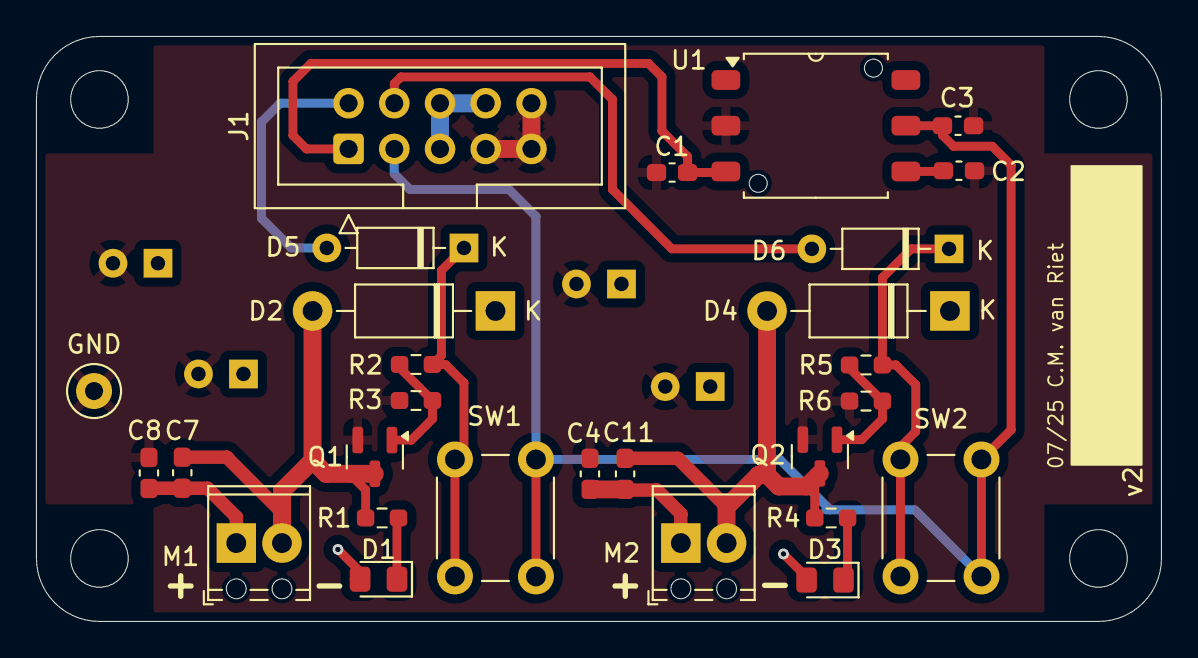
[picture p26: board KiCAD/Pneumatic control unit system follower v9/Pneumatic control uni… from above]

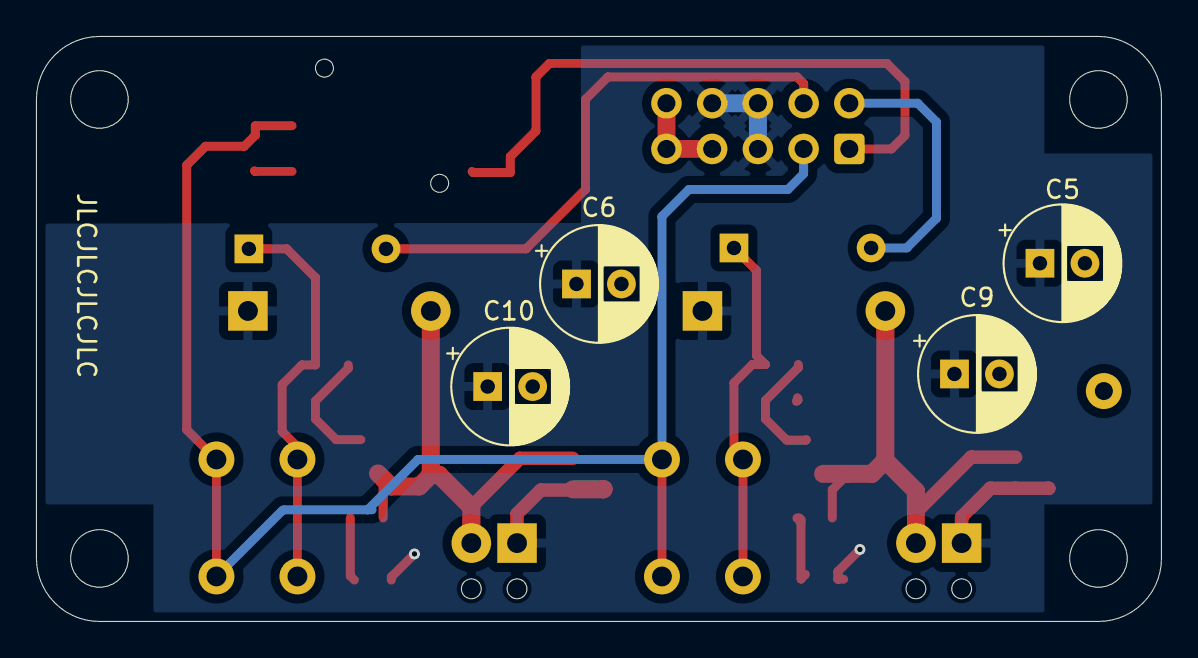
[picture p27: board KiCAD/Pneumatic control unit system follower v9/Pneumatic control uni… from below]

Board: 2 copper layers, 62.5 x 32.5 mm, 32 parts (4 on the bottom side), 15 nets.

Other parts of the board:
GND: TestPoint_Loop_D2.50mm_Drill1.0mm

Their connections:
GND: GND.1; also elsewhere on the board

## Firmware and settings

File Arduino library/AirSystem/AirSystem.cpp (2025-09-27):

#include "AirSystem.h"

// ------------------- Pump -------------------
void Pump::begin(int pumpPin) {
  pin = pumpPin;
  pinMode(pin, OUTPUT);
  off();
}

void Pump::set(float percentage) {
  if (percentage < 0) percentage = 0;
  if (percentage > 100) percentage = 100;
  int pwmValue = map((int)percentage, 0, 100, 0, 255);
  analogWrite(pin, pwmValue);
}

void Pump::on() {
  analogWrite(pin, 255);
}

void Pump::off() {
  analogWrite(pin, 0);
}

// ------------------- Valve -------------------
void Valve::begin(int valvePin) {
  pin = valvePin;
  pinMode(pin, OUTPUT);
  close();
}

void Valve::open() {
  digitalWrite(pin, HIGH);
}

void Valve::close() {
  digitalWrite(pin, LOW);
}

// ------------------- Sensor -------------------
void Sensor::begin(int sensorPin) {
  pin = sensorPin;
  pinMode(pin, INPUT);
}

float Sensor::read() {
  float pressure = 0.219 * analogRead(pin) - 7.664;     // Pressure in kPa
  return pressure;
}

// ------------------- Global objects -------------------

// Arrays of real objects
Pump pumps[CHANNEL_COUNT];
Valve valves[CHANNEL_COUNT];
Sensor sensors[CHANNEL_COUNT];

// Named references bound to array elements
Pump& pumpA = pumps[0];
Pump& pumpB = pumps[1];
Pump& pumpC = pumps[2];
Pump& pumpD = pumps[3];

Valve& valveA = valves[0];
Valve& valveB = valves[1];
Valve& valveC = valves[2];
Valve& valveD = valves[3];

Sensor& sensorA = sensors[0];
Sensor& sensorB = sensors[1];
Sensor& sensorC = sensors[2];
Sensor& sensorD = sensors[3];

// ------------------- Init function -------------------
void AirSystem_begin() {
  int pumpPins[CHANNEL_COUNT]   = PUMP_PINS;
  int valvePins[CHANNEL_COUNT]  = VALVE_PINS;
  int sensorPins[CHANNEL_COUNT] = SENSOR_PINS;

  for (int i = 0; i < CHANNEL_COUNT; i++) {
    pumps[i].begin(pumpPins[i]);
    valves[i].begin(valvePins[i]);
    sensors[i].begin(sensorPins[i]);
  }
}

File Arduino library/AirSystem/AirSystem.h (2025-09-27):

#ifndef AIRSYSTEM_H
#define AIRSYSTEM_H

#include <Arduino.h>

#define CHANNEL_COUNT 4

#define PUMP_PINS   {15, 13, 11, 9}
#define VALVE_PINS  {14, 12, 10, 8}
#define SENSOR_PINS {29, 28, 27, 26}
#define LED_BUILTIN 16

// ---- Pump ---- //
class Pump {
  int pin;
public:
  Pump() {}
  Pump(int pumpPin) { begin(pumpPin); }
  void begin(int pumpPin);
  void set(float percentage);
  void on();
  void off();
};

// ---- Valve ---- //
class Valve {
  int pin;
public:
  Valve() {}
  Valve(int valvePin) { begin(valvePin); }
  void begin(int valvePin);
  void open();
  void close();
};

// ---- Sensor ---- //
class Sensor {
  int pin;
public:
  Sensor() {}
  Sensor(int sensorPin) { begin(sensorPin); }
  void begin(int sensorPin);
  float read();
};

// ---- Global arrays ---- //
extern Pump pumps[CHANNEL_COUNT];
extern Valve valves[CHANNEL_COUNT];
extern Sensor sensors[CHANNEL_COUNT];

// ---- Named references ---- //
extern Pump& pumpA;
extern Pump& pumpB;
extern Pump& pumpC;
extern Pump& pumpD;

extern Valve& valveA;
extern Valve& valveB;
extern Valve& valveC;
extern Valve& valveD;

extern Sensor& sensorA;
extern Sensor& sensorB;
extern Sensor& sensorC;
extern Sensor& sensorD;

// ---- Init function ---- //
void AirSystem_begin();

#endif

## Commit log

2025-09-27 first upload
    [Leader v9.step, Pneumatic control unit system broad.step, Pneumatic control unit system follower.csv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]
2025-09-27 Update clear buttons.jpg
2025-09-28 added schematics
